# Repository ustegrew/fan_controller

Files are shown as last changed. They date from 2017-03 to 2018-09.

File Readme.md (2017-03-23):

# Ventilator control for a laundry

A control system for a fan in a laundry drying room, to exchange humid air for dry air from outside.

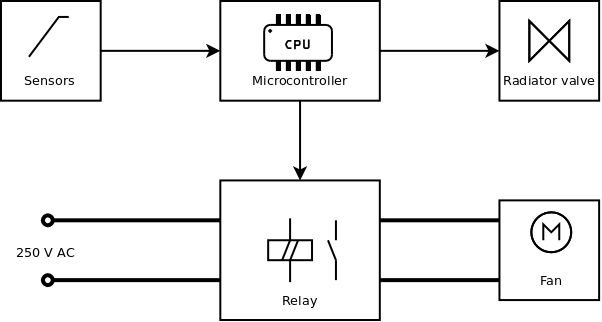
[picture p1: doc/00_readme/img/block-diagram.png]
Block diagram


## Repository structure

  * [Documentation::Wiki](https://github.com/ustegrew/fan_controller/wiki)
  * [Documentation::Files](https://github.com/ustegrew/fan_controller/tree/master/doc).

## Licenses

Source code is licensed under GPL3, all other content under FDL.

### Source code

    This program is free software: you can redistribute it and/or modify
    it under the terms of the GNU General Public License as published by
    the Free Software Foundation, either version 3 of the License, or
    (at your option) any later version.
	
    This program is distributed in the hope that it will be useful,
    but WITHOUT ANY WARRANTY; without even the implied warranty of
    MERCHANTABILITY or FITNESS FOR A PARTICULAR PURPOSE.  See the
    GNU General Public License for more details.
    
	You should have received a copy of the GNU General Public License
    along with this program.  If not, see <http://www.gnu.org/licenses/>.

### All other content

        Copyright (c)  2017  PETER HOPPE.
    Permission is granted to copy, distribute and/or modify this document
    under the terms of the GNU Free Documentation License, Version 1.3
    or any later version published by the Free Software Foundation;
    with no Invariant Sections, no Front-Cover Texts, and no Back-Cover Texts.
    A copy of the license is included in the section entitled "GNU
    Free Documentation License".

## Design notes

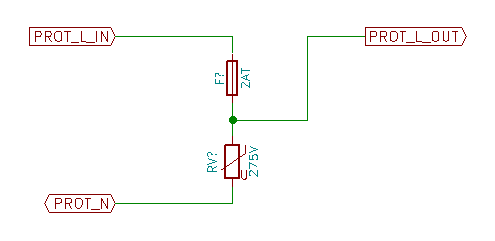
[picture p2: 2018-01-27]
schematics/controller/img/varistor-protection-module.png

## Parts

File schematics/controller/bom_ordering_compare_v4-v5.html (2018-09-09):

Article | Ref | Qnty | Value | Description
 | A15001 | 1 | Arduino_Nano_v3.x | Arduino Nano v3.x
Mouser::80-EST108M063AM3AA | C3001 | 1 | 1000uF/63V | Polarised capacitor
Mouser::594-MAL225098475E3 | C3002, C3006, C3010 | 3 | 470uF/63V | Polarised capacitor
Mouser::810-C3216C0G2A104J16 | C3003, C3007, C3008, C6002, C6003, C6006, C6007, C7002, C7003, C7005, C7008, C9002, C9003, C9006, C9007, C10002, C10003, C10005, C10008, C11005, C11006, C11013, C11014, C12001, C12002, C12003, C12005, C12006, C12007, C13001, C13004 | 31 | 100nF | Unpolarized capacitor
Mouser::810-C3216JB2A105K16A | C3004, C3005, C3009, C6008, C9008, C12009, C12010 | 7 | 1uF | Unpolarized capacitor
Mouser::667-EEU-EB1J470B | C5001, C5002, C7001, C7004, C8001, C8002, C10001, C10004, C11015, C11016, C12011, C12012, C13007, C13008 | 14 | 47uF / 63V | Polarised capacitor
Mouser::80-C1812C242GCG | C6001, C6005 | 2 | 2.4nF | Unpolarized capacitor
Mouser::810-C3225X7S2A475KST | C6004, C7006, C7007, C7009, C7010, C9004, C10006, C10007, C10009, C10010, C11007, C11012, C13002, C13005 | 14 | 4.7uF | Unpolarized capacitor
Mouser::80-C1206C474K1RAUTO | C6009, C9009 | 2 | 0.47uF | Unpolarized capacitor
Mouser::80-C2220C102FCG | C9001, C9005, C11001, C11002, C11004, C11008, C11009, C11011 | 8 | 1nF | Unpolarized capacitor
Mouser::80-C1206C911FBGACTU | C11003, C11010 | 2 | 910pF | Unpolarized capacitor
Mouser:: 80-C0805C224J1RECTU | C12004 | 1 | 0.22uF | Unpolarized capacitor
Mouser:: 80-C0805C393K1RAUTO | C12008 | 1 | 39nF | Unpolarized capacitor
Mouser::605-502S47W472KV4E | C13003, C13006 | 2 | 4.7nF | Unpolarized capacitor
Mouser::750-1.5KE33CA-G | D1001, D1002, D1003, D1004, D1005, D1006, D1007, D1008, D1009 | 9 | 1.5KE33CA | Bidirectional transient-voltage-suppression (TVS) diode
Mouser::78-1.5KE30CAHE3_A/C | D1010, D1011, D1012, D1013, D1014, D1015, D1016, D1017, D1018 | 9 | 1.5KE30CA | Bidirectional transient-voltage-suppression (TVS) diode
Mouser::78-1N4148W-E3-18 | D2001, D6001, D6002, D7003, D9001, D9002, D10003, D12002, D12003, D12004, D14001 | 11 | 1N4148 | 100V 0.15A standard switching diode, DO-35
Mouser::78-1.5KE36CAHE3_A/C | D3001, D3004, D3007, D3009, D3012, D3015, D3020, D3024 | 8 | 1.5KE36CA | Bidirectional transient-voltage-suppression (TVS) diode
Mouser::625-1N5404-E3 | D3002, D3003, D3005, D3006, D3010, D3011, D3013, D3014, D3018, D3019, D3021, D3022 | 12 | 1N5404 | 50V 3A General Purpose Rectifier Diode, DO-201AD
Mouser::621-1N4007G-T | D3008, D3016, D3023 | 3 | 1N4007 | 50V 1A General Purpose Rectifier Diode, DO-41
Mouser::625-BZX85C5V6 | D7001, D7002, D7004, D10001, D10002, D10004 | 6 | BZX85C5V6 | Zener Diode
Mouser::625-BZX85C6V2 | D12001 | 1 | BZX85C6V2 | z-diode, bzx85 series
Mouser::625-1.5KE12CA-E3 | D13001, D13002, D13003 | 3 | 1.5KE12CA | Bidirectional transient-voltage-suppression (TVS) diode
Mouser::576-64600001003 | F1001, F1002, F1003, F1004, F1005, F1006 | 6 | 250mAF | Fuse, generic
Mouser::576-64600001003 | F1007, F1008, F1009, F1010, F1011, F1012 | 6 | 100mAF | Fuse, generic
Mouser::534-4525 | F2001 | 1 | 6AT | Fuse, generic
Mouser::576-64600001003 | F3001, F3002 | 2 | 2AT | Fuse, generic
Mouser::576-64600001003 | F3003, F3004 | 2 | 1AT | Fuse, generic
Mouser::576-64600001003 | F3005, F3006, F3007, F3008 | 4 | 1AF | Fuse, generic
Mouser::651-5430373 | J1001, J1002 | 2 | Screw_Terminal_01x03 | Generic screw terminal, single row, 01x03
Mouser::651-1935268 | J1003 | 1 | Periphery | Generic screw terminal, single row, 01x12
Mouser::571-1969799-1 | J1004 | 1 | Conn_01x02_Male | Generic connector, single row, 01x02
Mouser::571-1969807-1 | J1005, J1006 | 2 | Conn_01x04_Male | Generic connector, single row, 01x04
Mouser::571-6404565 | J1007 | 1 | FRONTPANEL | Generic connector, single row, 01x05
Mouser::655-RT424024 | K2001 | 1 | TE RT424024 | General Purpose Relays DPDT 8A 24VDC PCB
inherent | MK1001, MK1002, MK1003, MK1004, MK1005, MK1006, MK1007, MK1008, MK1009, MK1010 | 10 | 3.5 | Mounting Hole with connection
Mouser::512-BC556BTA | Q2001, Q7004, Q10004, Q12001, Q12002 | 5 | BC556 | 45V Vce, 0.1A Ic, PNP Small Signal Transistor, TO-92
Mouser::512-BC546CTA | Q2002, Q7001, Q7002, Q7003, Q10001, Q10002, Q10003, Q12003, Q12004, Q12005, Q12006, Q12007, Q12008, Q14001, Q14002, Q14003, Q14004, Q14005, Q15001 | 19 | BC546C | 45V Vce, 0.1A Ic, NPN, Small Signal Transistor, TO-92
Mouser::863-BD243CG | Q2003 | 1 | BD243C | 25A Ic, 55V Vce, Silicon Power Transistors NPN, SOT-93
Not Mouser | Q6001, Q9001 | 2 | 2N3819 | Transistor N-JFET (general)
Mouser::594-AC01W27R00J | R1001, R1002, R1003, R1004, R1005, R1006 | 6 | 27Ω / 1W | Resistor
Mouser::71-TNPU0805100KAZEN | R2001, R2005, R7005, R7006, R7008, R7009, R7016, R10005, R10006, R10008, R10009, R10016, R11003, R12009, R12010, R12013, R12017, R12018, R13004, R13005, R14002, R14003, R14007, R14009, R14010 | 25 | 100kΩ | Resistor
Mouser::71-TNPU080510K0AZEN | R2002, R2003, R7002, R7003, R7004, R7007, R10002, R10003, R10004, R10007, R13001, R13002, R14001, R14004, R14005, R14006, R14008, R15001, R15002, R15003, R15004, R15005, R15006, R15007 | 24 | 10kΩ | Resistor
Mouser::594-MCU08050C4701FP5 | R2004, R6003, R6004, R7001, R7010, R9003, R9004, R10001, R10010, R12001 | 10 | 4.7kΩ | Resistor
Mouser::71-TNPW06034K42BEEA | R6001, R6002 | 2 | 4.42kΩ | Resistor
Mouser::71-TNPU08051K00BZEN | R7011, R7012, R7013, R7014, R7015, R10011, R10012, R10013, R10014, R10015 | 10 | 1kΩ | Resistor
Mouser::71-TNPW06036K34BEEN | R9001, R9002 | 2 | 6.34kΩ | Resistor
Mouser::71-TNPW0603118KBEEN | R11001, R11004 | 2 | 118kΩ | Resistor
Mouser::71-TNPW0603133KBEEN | R11002 | 1 | 133kΩ | Resistor
Mouser::71-TNPU080549K9BZEN | R11005 | 1 | 49.9kΩ | Resistor
Mouser::71-TNPW060356K2BEEA | R11006 | 1 | 56.2kΩ | Resistor
Mouser::71-TNPW060339K2BEEN | R11007 | 1 | 39.2kΩ | Resistor
Mouser::71-TNPW060346K4BEEA | R11008 | 1 | 46.4kΩ | Resistor
Mouser::71-TNPW0603825RBEEA | R11009 | 1 | 825Ω | Resistor
Mouser::71-TNPW0603931RBEEN | R11010 | 1 | 931Ω | Resistor
Mouser::71-TNPW06031K05BEEA | R11011 | 1 | 1.05kΩ | Resistor
Mouser::71-TNPW060323K7BEEN | R11012 | 1 | 23.7kΩ | Resistor
Mouser::71-TNPW06031K21BEEN | R11013 | 1 | 1.21kΩ | Resistor
Mouser::71-TNPW060327K4BEEN | R11014 | 1 | 27.4kΩ | Resistor
Mouser::71-TNPW0603316RBEEN | R11015 | 1 | 316Ω | Resistor
Mouser::71-TNPW0603357RBEEA | R11016 | 1 | 357Ω | Resistor
Mouser::71-TNPW060368K0BEEA | R12002 | 1 | 68kΩ | Resistor
Mouser::71-TNPW060322K0BEEN | R12003, R12004, R12006, R12007, R12008 | 5 | 22kΩ | Resistor
Mouser::71-TNPW06037K50BEEN | R12005 | 1 | 7.5kΩ | Resistor
Mouser::71-TNPW060339K0BEEA | R12011, R12012, R12014, R12015, R12016, R12019 | 6 | 39kΩ | Resistor
Mouser::71-TNPW0603220RBEEA | R13003, R13006 | 2 | 220Ω | Resistor
Mouser::652-3296W-1-223LF | RV6001, RV6002, RV9001, RV9002, RV12001, RV13001, RV13002 | 7 | 22kΩ | Potentiometer
alreadyHere::Mouser::983-T60403-K5032X102 | T13001 | 1 | Transformer_2P_1S | Transformer, single primary, dual secondary
Mouser::571-1969803-1 | U1001 | 1 | Module: surgeprot.mains.275.5.01
Mouser::652-2026-07-C2LF | U1002, U1003, U1004 | 3 | Bourns 2026-07-C2LF | Gas discharge tube
Mouser::511-L7805ABV | U3001 | 1 | L7805 | Positive 1.5A 35V Linear Regulator, Fixed Output 5V, TO-220/TO-263/TO-252
Mouser::511-L7815ABV | U3002 | 1 | L7815 | Positive 1.5A 35V Linear Regulator, Fixed Output 5V, TO-220/TO-263/TO-252
Mouser::511-L7915ACV | U3003 | 1 | L7915 | Negative 1.5A 35V Linear Regulator, Fixed Output -5V, TO-220/TO-263
Mouser::595-TL061CDR | U6001, U6002, U7002, U9001, U9002, U10002, U12001, U12002, U12003 | 9 | TL061 | Operational Amplifier, DIP-8/TO-99-8
Mouser::595-CD4066BM96 | U7001, U10001 | 2 | 4066 | Quad Analog Switches
Mouser::584-OP282GSZ | U11001, U11002, U13001 | 3 | OP282 | Dual/Quad, Low Power, High Speed JFET Operational Amplifiers
Ref | Qnty | Value | Part | Footprint | Description | Vendor
A15001 | 1 | Arduino_Nano_v3.x | modules:Arduino_Nano_v3.x | footprints:arduino-nano_3.x | Arduino Nano v3.x
C3001 | 1 | 1000uF/63V | Device:CP | Capacitors_THT:CP_Radial_D16.0mm_P7.50mm | Polarised capacitor
C3002, C3006, C3010 | 3 | 470uF/63V | Device:CP | Capacitors_THT:CP_Radial_D16.0mm_P7.50mm | Polarised capacitor
C3003, C3007, C3008, C6002, C6003, C6006, C6007, C7002, C7003, C7005, C7008, C9002, C9003, C9006, C9007, C10002, C10003, C10005, C10008, C11005, C11006, C11013, C11014, C12001, C12002, C12003, C12005, C12006, C12007, C13001, C13004 | 31 | 100nF | Device:C | Capacitors_SMD:C_1206_HandSoldering | Unpolarized capacitor
C3004, C3005, C3009, C6008, C9008, C12009, C12010 | 7 | 1uF | Device:C | Capacitors_SMD:C_1206_HandSoldering | Unpolarized capacitor
C5001, C5002, C7001, C7004, C8001, C8002, C10001, C10004, C11015, C11016, C12011, C12012, C13007, C13008 | 14 | 47uF / 63V | Device:CP | Capacitors_THT:CP_Radial_D8.0mm_P5.00mm | Polarised capacitor
C6001, C6005 | 2 | 2.4nF | Device:C | Capacitors_SMD:C_1812_HandSoldering | Unpolarized capacitor
C6004, C7006, C7007, C7009, C7010, C9004, C10006, C10007, C10009, C10010, C11007, C11012, C13002, C13005 | 14 | 4.7uF | Device:C | Capacitors_SMD:C_1210_HandSoldering | Unpolarized capacitor
C6009, C9009 | 2 | 0.47uF | Device:C | Capacitors_SMD:C_1206_HandSoldering | Unpolarized capacitor
C9001, C9005, C11001, C11002, C11004, C11008, C11009, C11011 | 8 | 1nF | Device:C | Capacitors_SMD:C_2220_HandSoldering | Unpolarized capacitor
C11003, C11010 | 2 | 910pF | Device:C | Capacitors_SMD:C_1206_HandSoldering | Unpolarized capacitor
C12004 | 1 | 0.22uF | Device:C | Capacitors_SMD:C_0805_HandSoldering | Unpolarized capacitor
C12008 | 1 | 39nF | Device:C | Capacitors_SMD:C_0805_HandSoldering | Unpolarized capacitor
C13003, C13006 | 2 | 4.7nF | Device:C | Capacitors_SMD:C_2220_HandSoldering | Unpolarized capacitor
D1001, D1002, D1003, D1004, D1005, D1006, D1007, D1008, D1009 | 9 | 1.5KE33CA | Device:D_TVS | Diodes_THT:D_DO-201AD_P12.70mm_Horizontal | Bidirectional transient-voltage-suppression (TVS) diode
D1010, D1011, D1012, D1013, D1014, D1015, D1016, D1017, D1018 | 9 | 1.5KE30CA | Device:D_TVS | Diodes_THT:D_DO-201AD_P12.70mm_Horizontal | Bidirectional transient-voltage-suppression (TVS) diode
D2001, D6001, D6002, D7003, D9001, D9002, D10003, D12002, D12003, D12004, D14001 | 11 | 1N4148 | diode:1N4148 | Diodes_SMD:D_SOD-123 | 100V 0.15A standard switching diode, DO-35
D3001, D3004, D3007, D3009, D3012, D3015, D3020, D3024 | 8 | 1.5KE36CA | Device:D_TVS | Diodes_THT:D_DO-201AD_P12.70mm_Horizontal | Bidirectional transient-voltage-suppression (TVS) diode
D3002, D3003, D3005, D3006, D3010, D3011, D3013, D3014, D3018, D3019, D3021, D3022 | 12 | 1N5404 | diode:1N5404 | Diodes_THT:D_DO-201AD_P12.70mm_Horizontal | 400V 3A General Purpose Rectifier Diode, DO-201AD
D3008, D3016, D3023 | 3 | 1N4007 | diode:1N4007 | Diodes_THT:D_DO-41_SOD81_P7.62mm_Horizontal | 1000V 1A General Purpose Rectifier Diode, DO-41
D7001, D7002, D7004, D10001, D10002, D10004 | 6 | BZX85C5V6 | Device:D_Zener | Diodes_THT:D_DO-41_SOD81_P7.62mm_Horizontal | Zener Diode
D12001 | 1 | BZX85C6V2 | fan-controller_parts:BZX85xx | Diodes_THT:D_DO-41_SOD81_P7.62mm_Horizontal | z-diode, bzx85 series
D13001, D13002, D13003 | 3 | 1.5KE12CA | Device:D_TVS | Diodes_THT:D_DO-201AD_P12.70mm_Horizontal | Bidirectional transient-voltage-suppression (TVS) diode
F1001, F1002, F1003, F1004, F1005, F1006 | 6 | 250mAF | Device:Fuse | Fuse_Holders_and_Fuses:Fuseholder5x20_horiz_open_Schurter_0031_8201 | Fuse, generic
F1007, F1008, F1009, F1010, F1011, F1012 | 6 | 100mAF | Device:Fuse | Fuse_Holders_and_Fuses:Fuseholder5x20_horiz_open_Schurter_0031_8201 | Fuse, generic
F2001 | 1 | 6AT | Device:Fuse | Wire_Connections_Bridges:WireConnection_2.50mmDrill_LargePad | Fuse, generic
F3001, F3002 | 2 | 2AT | Device:Fuse | Fuse_Holders_and_Fuses:Fuseholder5x20_horiz_open_Schurter_0031_8201 | Fuse, generic
F3003, F3004 | 2 | 1AT | Device:Fuse | Fuse_Holders_and_Fuses:Fuseholder5x20_horiz_open_Schurter_0031_8201 | Fuse, generic
F3005, F3006, F3007, F3008 | 4 | 1AF | Device:Fuse | Fuse_Holders_and_Fuses:Fuseholder5x20_horiz_open_Schurter_0031_8201 | Fuse, generic
J1001, J1002 | 2 | Screw_Terminal_01x03 | conn:Screw_Terminal_01x03 | Connectors_Phoenix:PhoenixContact_MSTBVA-G_03x5.00mm_Vertical | Generic screw terminal, single row, 01x03
J1003 | 1 | Periphery | conn:Screw_Terminal_01x12 | Connectors_Phoenix:PhoenixContact_MSTBVA-G_12x5.00mm_Vertical | Generic screw terminal, single row, 01x12
J1004 | 1 | Conn_01x02_Male | conn:Conn_01x02_Male | footprints:TE_1969799-1 | Generic connector, single row, 01x02
J1005, J1006 | 2 | Conn_01x04_Male | conn:Conn_01x04_Male | footprints:TE_1969807-1 | Generic connector, single row, 01x04
J1007 | 1 | FRONTPANEL | conn:Conn_01x05_Male | Pin_Headers:Pin_Header_Straight_1x05_Pitch2.54mm | Generic connector, single row, 01x05
K2001 | 1 | TE RT424024 (24VDC@1.44kOhm, DPDT, 250VAC, 8A) | relays:FINDER-44.62 | footprints:Relay_DPDT_Schrack-RT2-FormC_RM5.04mm | FINDER 44.62, Dual Pole Relay, 5mm Pitch, 10A
MK1001, MK1002, MK1003, MK1004, MK1005, MK1006, MK1007, MK1008, MK1009, MK1010 | 10 | 3.5 | mechanical:Mounting_Hole_PAD | Mounting_Holes:MountingHole_3.5mm_Pad_Via | Mounting Hole with connection
Q2001, Q7004, Q10004, Q12001, Q12002 | 5 | BC556 | Transistor_BJT:BC556 | TO_SOT_Packages_THT:TO-92_Inline_Wide | 0.1A Ic, 65V Vce, PNP Small Signal Transistor, TO-92
Q2002, Q7001, Q7002, Q7003, Q10001, Q10002, Q10003, Q12003, Q12004, Q12005, Q12006, Q12007, Q12008, Q14001, Q14002, Q14003, Q14004, Q14005, Q15001 | 19 | BC546C | transistors:BC546 | TO_SOT_Packages_THT:TO-92_Inline_Wide | 65V Vce, 0.1A Ic, NPN, Small Signal Transistor, TO-92
Q2003 | 1 | BD243C | transistors:BD249C | TO_SOT_Packages_THT:TO-220-3_Vertical | 25A Ic, 115V Vce, Silicon Power Transistors NPN, SOT-93
Q6001, Q9001 | 2 | 2N3819 | Device:Q_NJFET_DGS | TO_SOT_Packages_THT:TO-92_Inline_Wide | Transistor N-JFET (general)
R1001, R1002, R1003, R1004, R1005, R1006 | 6 | 27Ω / 1W | device:R | Resistors_THT:R_Axial_DIN0414_L11.9mm_D4.5mm_P15.24mm_Horizontal | Resistor
R2001, R2005, R7005, R7006, R7008, R7009, R7016, R10005, R10006, R10008, R10009, R10016, R11003, R12009, R12010, R12013, R12017, R12018, R13004, R13005, R14002, R14003, R14007, R14009, R14010 | 25 | 100kΩ | device:R | Resistors_SMD:R_0805_HandSoldering | Resistor
R2002, R2003, R7002, R7003, R7004, R7007, R10002, R10003, R10004, R10007, R13001, R13002, R14001, R14004, R14005, R14006, R14008, R15001, R15002, R15003, R15004, R15005, R15006, R15007 | 24 | 10kΩ | device:R | Resistors_SMD:R_0805_HandSoldering | Resistor
R2004, R6003, R6004, R7001, R7010, R9003, R9004, R10001, R10010, R12001 | 10 | 4.7kΩ | device:R | Resistors_SMD:R_0805_HandSoldering | Resistor
R6001, R6002 | 2 | 4.42kΩ | Device:R | Resistors_SMD:R_0603_HandSoldering | Resistor
R7011, R7012, R7013, R7014, R7015, R10011, R10012, R10013, R10014, R10015 | 10 | 1kΩ | Device:R | Resistors_SMD:R_0805_HandSoldering | Resistor
R9001, R9002 | 2 | 6.34kΩ | Device:R | Resistors_SMD:R_0603_HandSoldering | Resistor
R11001, R11004 | 2 | 118kΩ | device:R | Resistors_SMD:R_0603_HandSoldering | Resistor
R11002 | 1 | 133kΩ | device:R | Resistors_SMD:R_0603_HandSoldering | Resistor
R11005 | 1 | 49.9kΩ | device:R | Resistors_SMD:R_0805_HandSoldering | Resistor
R11006 | 1 | 56.2kΩ | device:R | Resistors_SMD:R_0603_HandSoldering | Resistor
R11007 | 1 | 39.2kΩ | device:R | Resistors_SMD:R_0603_HandSoldering | Resistor
R11008 | 1 | 46.4kΩ | device:R | Resistors_SMD:R_0603_HandSoldering | Resistor
R11009 | 1 | 825Ω | device:R | Resistors_SMD:R_0603_HandSoldering | Resistor
R11010 | 1 | 931Ω | device:R | Resistors_SMD:R_0603_HandSoldering | Resistor
R11011 | 1 | 1.05kΩ | device:R | Resistors_SMD:R_0603_HandSoldering | Resistor
R11012 | 1 | 23.7kΩ | device:R | Resistors_SMD:R_0603_HandSoldering | Resistor
R11013 | 1 | 1.21kΩ | device:R | Resistors_SMD:R_0603_HandSoldering | Resistor
R11014 | 1 | 27.4kΩ | device:R | Resistors_SMD:R_0603_HandSoldering | Resistor
R11015 | 1 | 316Ω | device:R | Resistors_SMD:R_0603_HandSoldering | Resistor
R11016 | 1 | 357Ω | device:R | Resistors_SMD:R_0603_HandSoldering | Resistor
R12002 | 1 | 68kΩ | device:R | Resistors_SMD:R_0603_HandSoldering | Resistor
R12003, R12004, R12006, R12007, R12008 | 5 | 22kΩ | device:R | Resistors_SMD:R_0603_HandSoldering | Resistor
R12005 | 1 | 7.5kΩ | device:R | Resistors_SMD:R_0603_HandSoldering | Resistor
R12011, R12012, R12014, R12015, R12016, R12019 | 6 | 39kΩ | device:R | Resistors_SMD:R_0603_HandSoldering | Resistor
R13003, R13006 | 2 | 220Ω | device:R | Resistors_SMD:R_0603_HandSoldering | Resistor
RV6001, RV6002, RV9001, RV9002, RV12001, RV13001, RV13002 | 7 | 22kΩ | device:POT_TRIM | Potentiometers:Potentiometer_Trimmer_Bourns_3296W | Trim-Potentiometer
T13001 | 1 | Transformer_2P_1S | Device:Transformer_1P_2S | fan-controller_parts:TRANSFORMER_VENDOR_VACUUMSCHMELZE_T60403-K5032-X102 | Transformer, single primary, dual secondary
U1001 | 1 | Module: surgeprot.mains.275.5.01 | fan-controller_parts:line-protector | footprints:TE_1969803-1
U1002, U1003, U1004 | 3 | Bourns 2026-07-C2LF | ESD_Protection:GDT-3 | footprints:Bourns_2026-xx | Gas discharge tube
U3001 | 1 | L7805 | regul:L7805 | Power_Integrations:TO-220 | Positive 1.5A 35V Linear Regulator, Fixed Output 5V, TO-220/TO-263/TO-252
U3002 | 1 | L7815 | regul:L7815 | Power_Integrations:TO-220 | Positive 1.5A 35V Linear Regulator, Fixed Output 15V, TO-220/TO-263/TO-252
U3003 | 1 | L7915 | regul:L7915 | Power_Integrations:TO-220 | Negative 1.5A 35V Linear Regulator, Fixed Output -15V, TO-220/TO-263
U6001, U6002, U7002, U9001, U9002, U10002, U12001, U12002, U12003 | 9 | TL061 | Amplifier_Operational:TL061 | Housings_SOIC:SOIC-8-1EP_3.9x4.9mm_Pitch1.27mm | Single Low-Power JFET-Input Operational Amplifiers, DIP-8/SOIC-8
U7001, U10001 | 2 | 4066 | 4xxx:4066 | Housings_SOIC:SOIC-14_3.9x8.7mm_Pitch1.27mm | Quad Analog Switches
U11001, U11002, U13001 | 3 | OP282 | fan-controller_parts:OP282 | Housings_SOIC:SOIC-8-1EP_3.9x4.9mm_Pitch1.27mm | Dual/Quad, Low Power, High Speed JFET Operational Amplifiers

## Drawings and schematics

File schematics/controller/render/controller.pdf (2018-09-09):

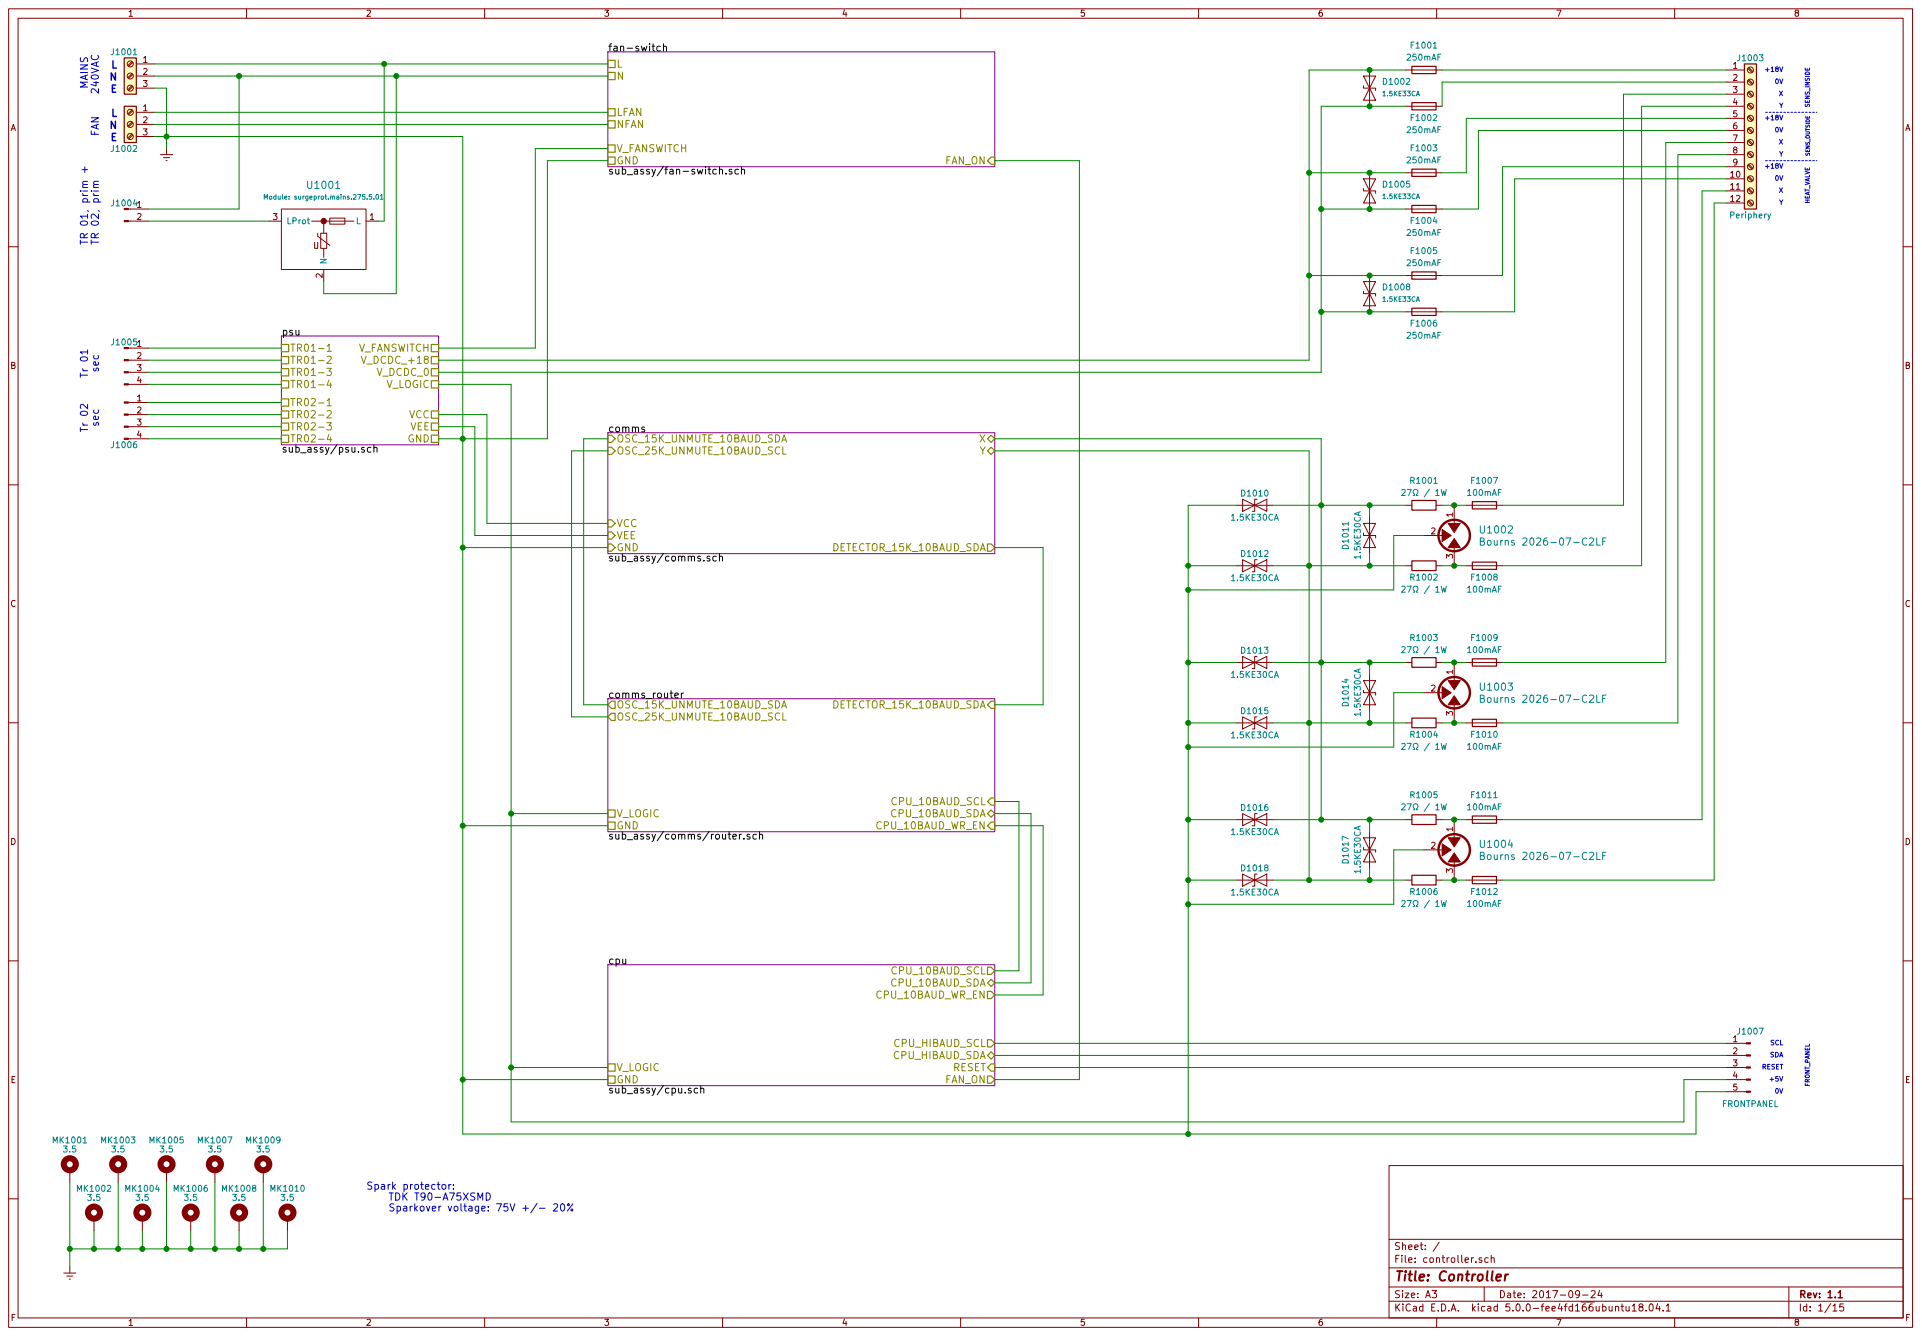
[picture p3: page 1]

Module: surgeprot.mains.275.5.01 MAINS 240VAC FAN

LN NFAN GND

10
11

100mAF D1016

Id: 1/15 Title: Controller File: controller.sch Sheet: /

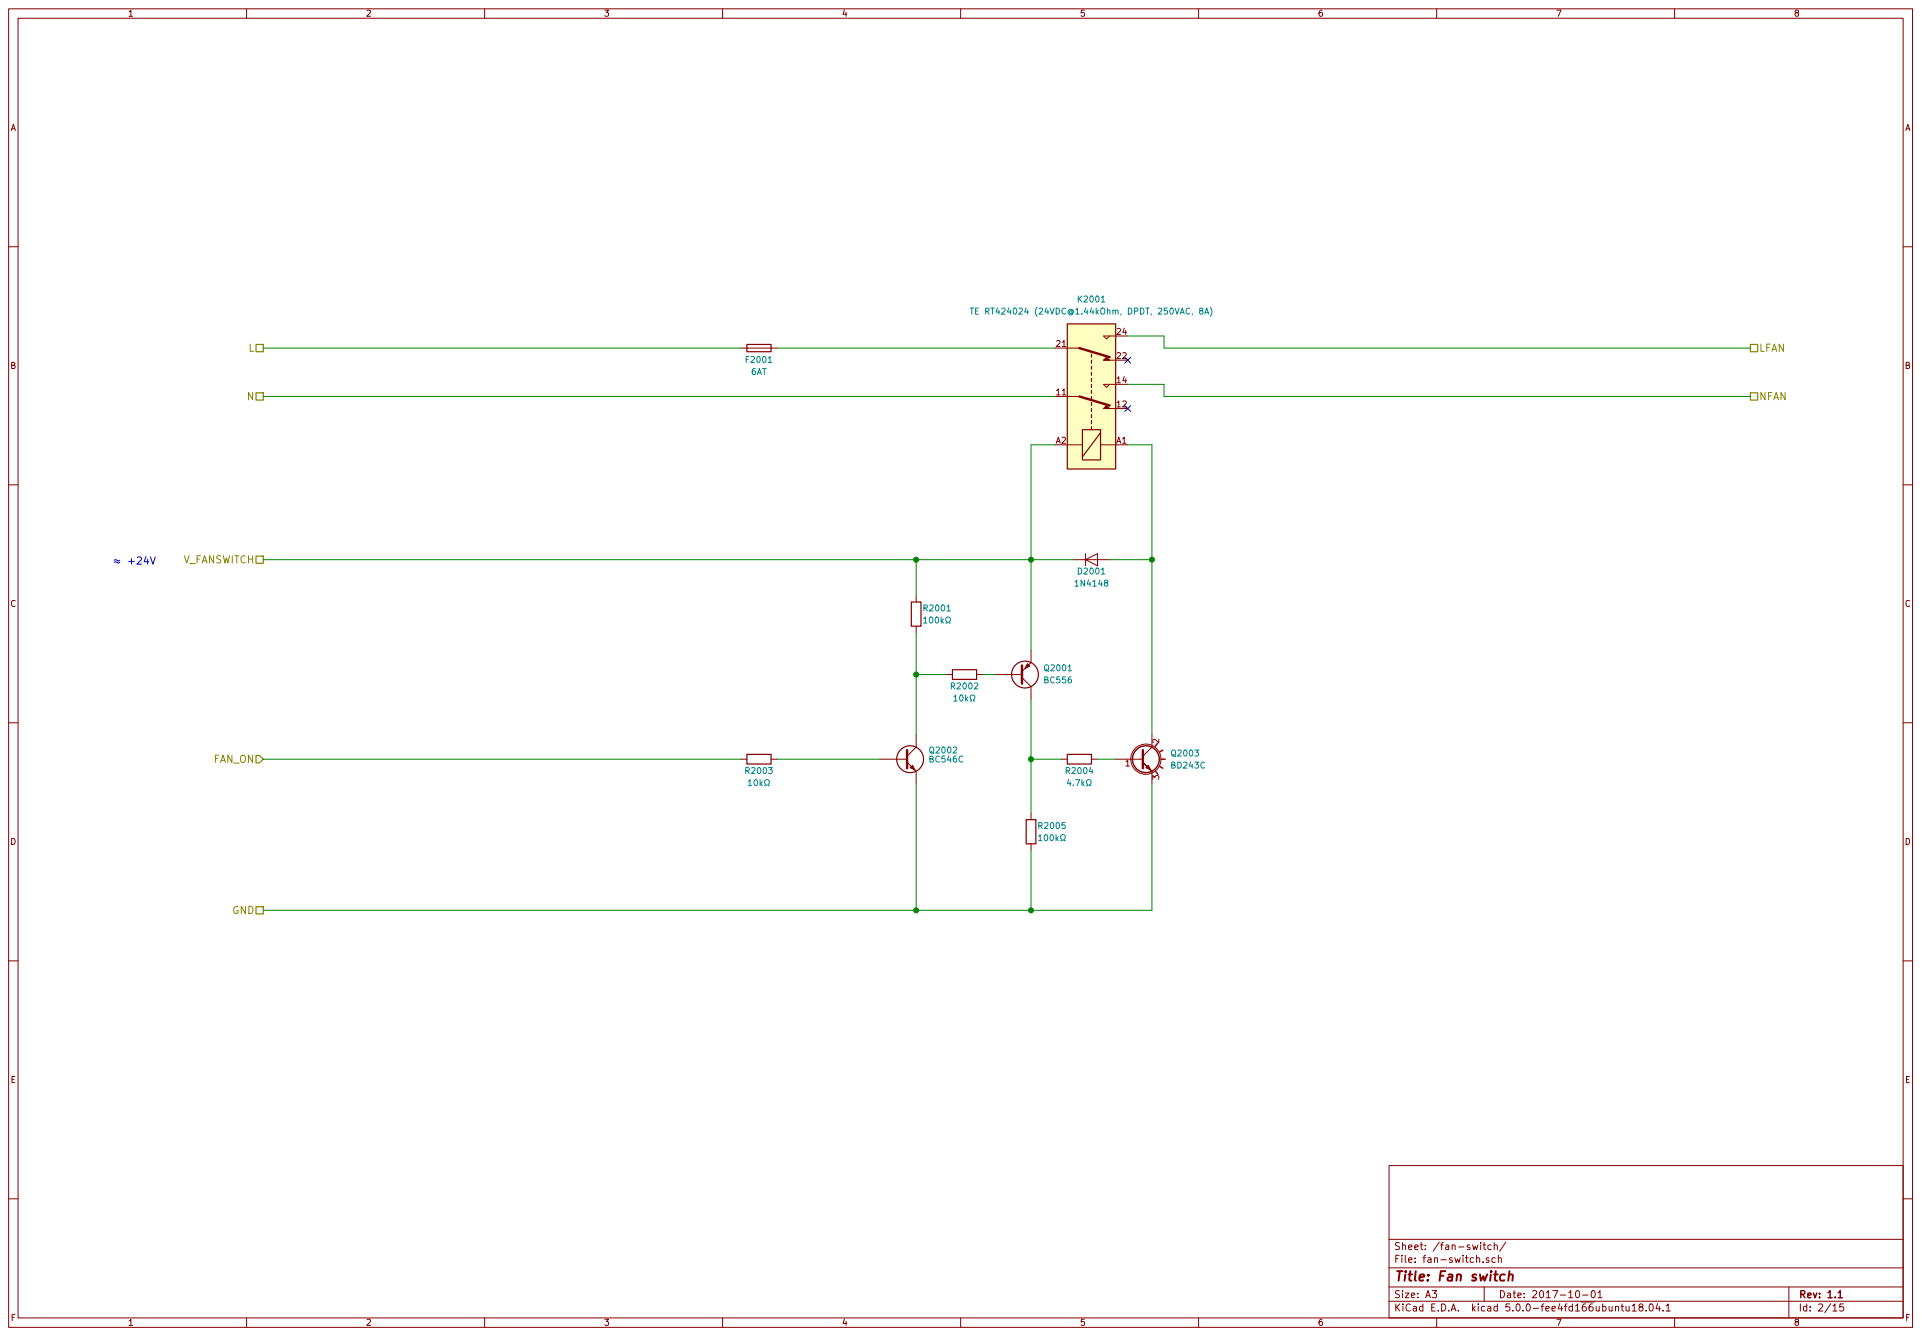
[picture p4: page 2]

File: fan-switch.sch Sheet: /fan-switch/
Id: 2/15 Title: Fan switch

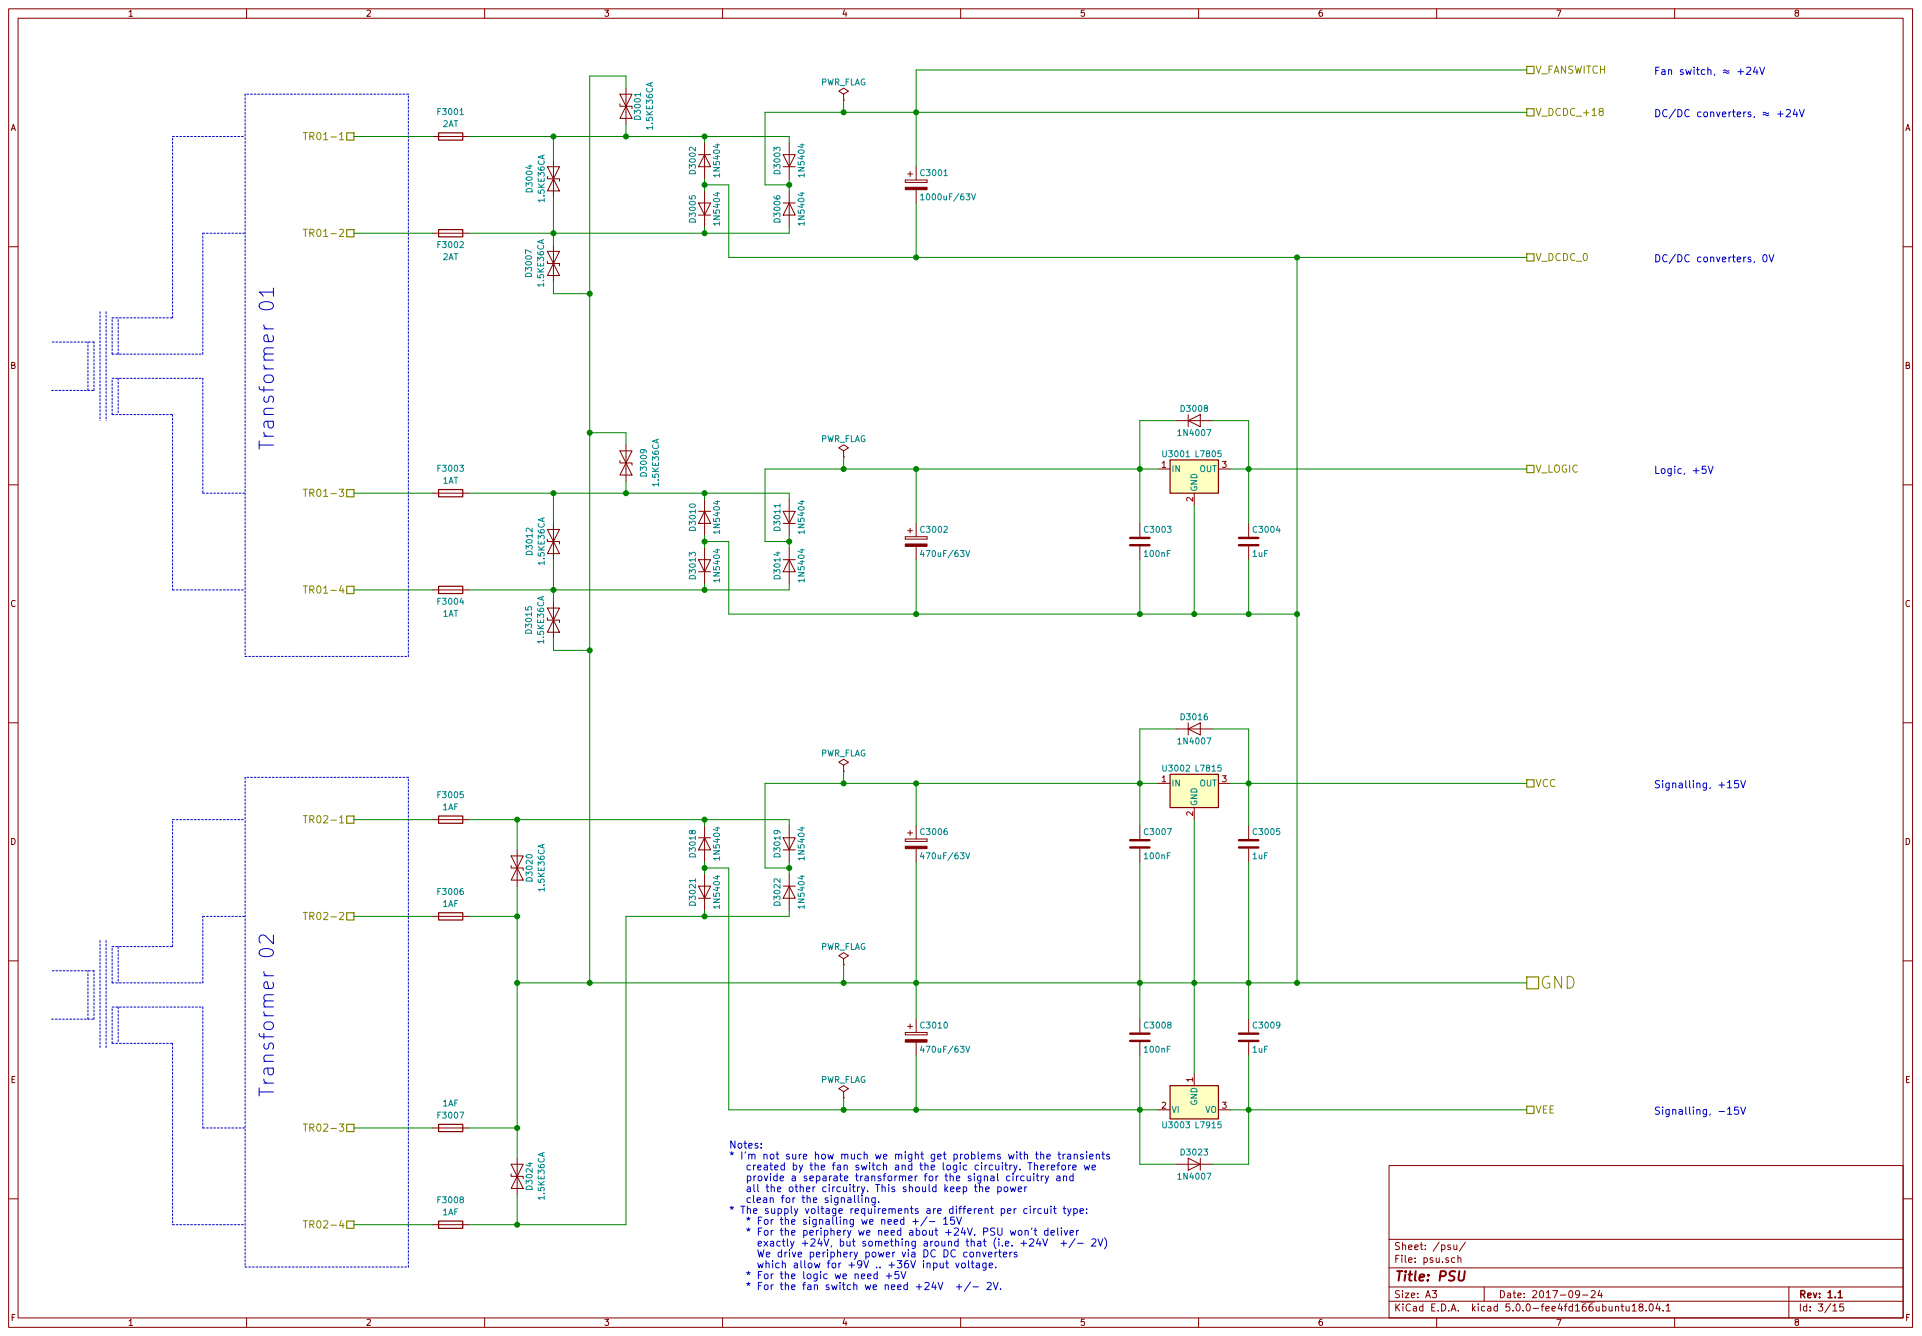
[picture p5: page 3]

PWR_FLAG Notes: * I'm not sure how much we might get problems with the transients

created by the fan switch and the logic circuitry. Therefore we
provide a separate transformer for the signal circuitry and
all the other circuitry. This should keep the power
clean for the signalling.
* The supply voltage requirements are different per circuit type:
* For the signalling we need +/- 15V
* For the periphery we need about +24V. PSU won't deliver
We drive periphery power via DC DC converters
which allow for +9V .. +36V input voltage.
* For the logic we need +5V
* For the fan switch we need +24V +/- 2V.

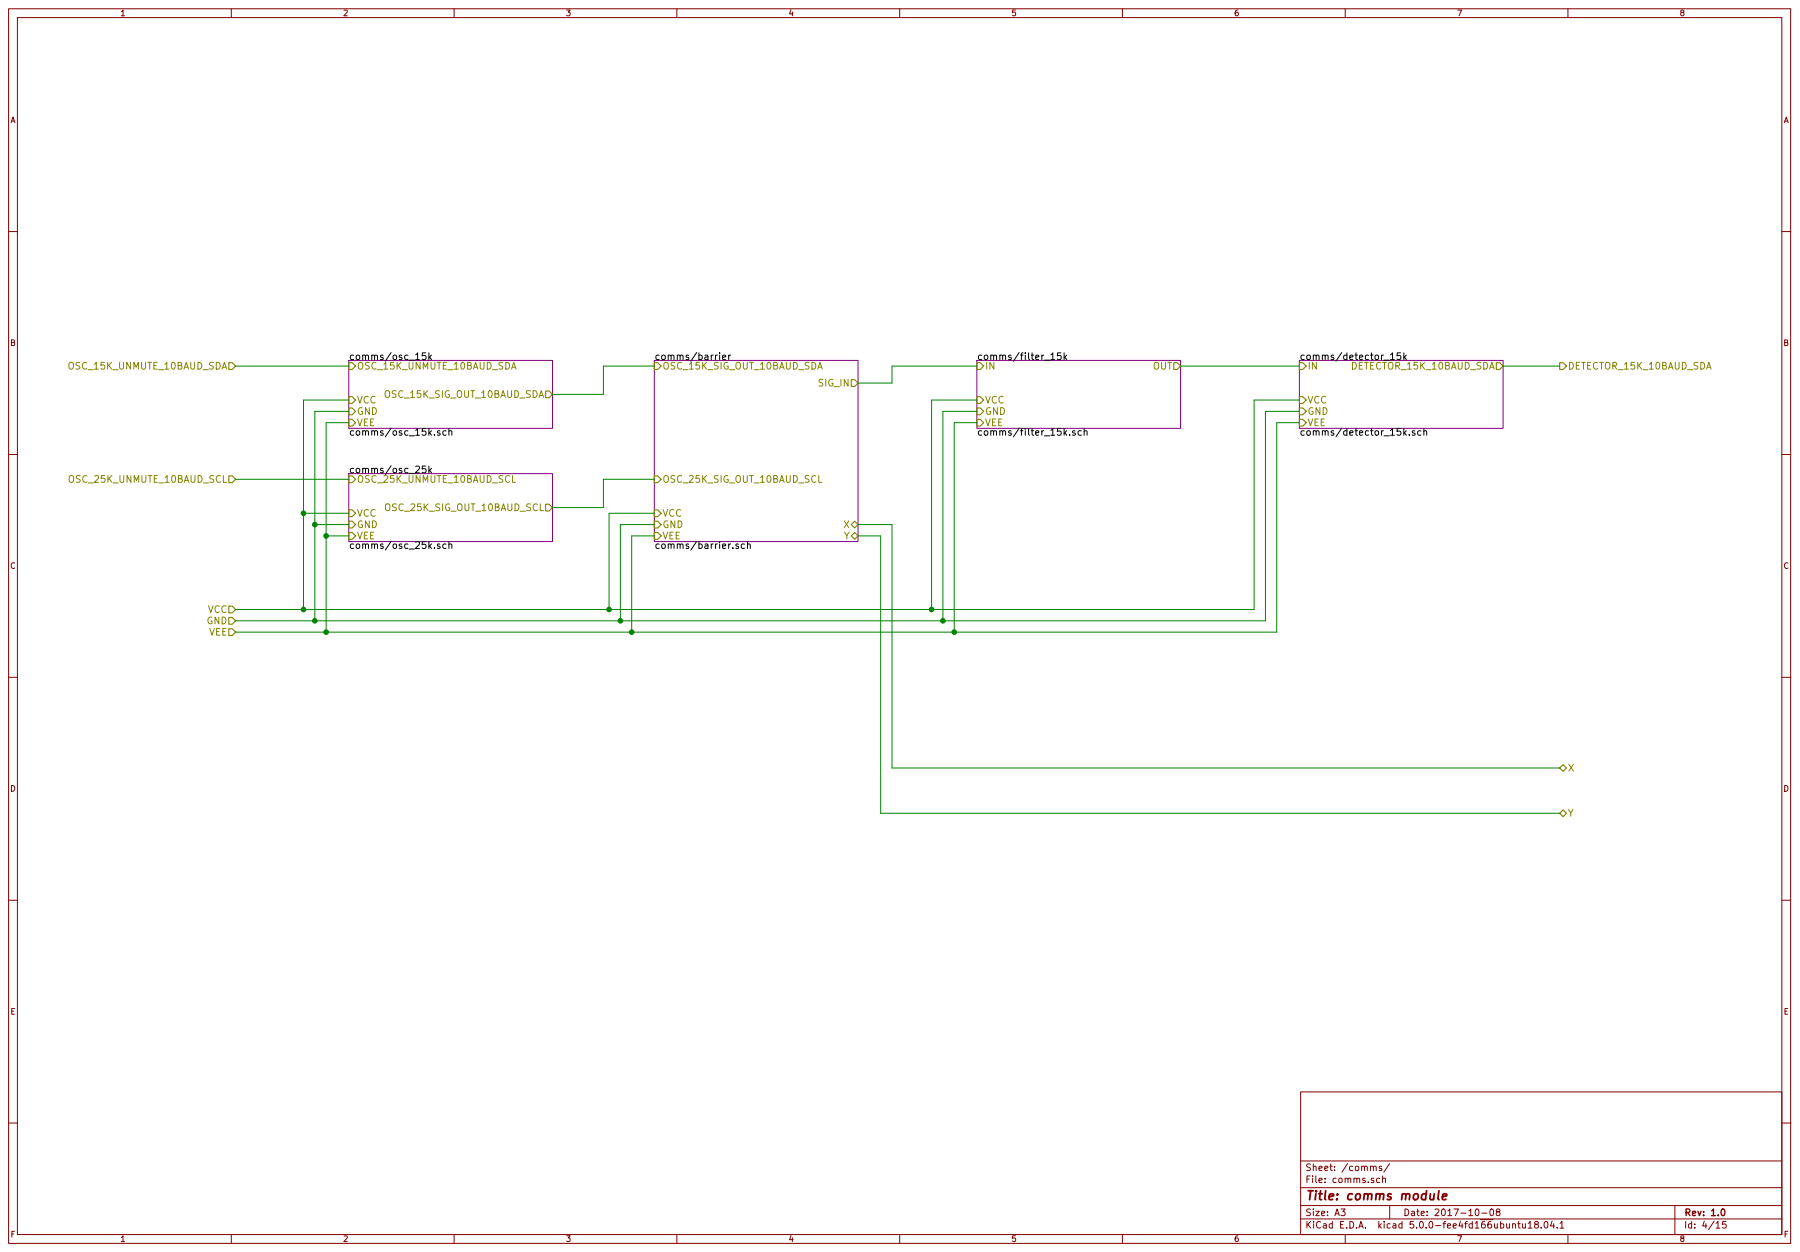
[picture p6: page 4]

File: comms.sch Sheet: /comms/
Id: 4/15 Title: comms module

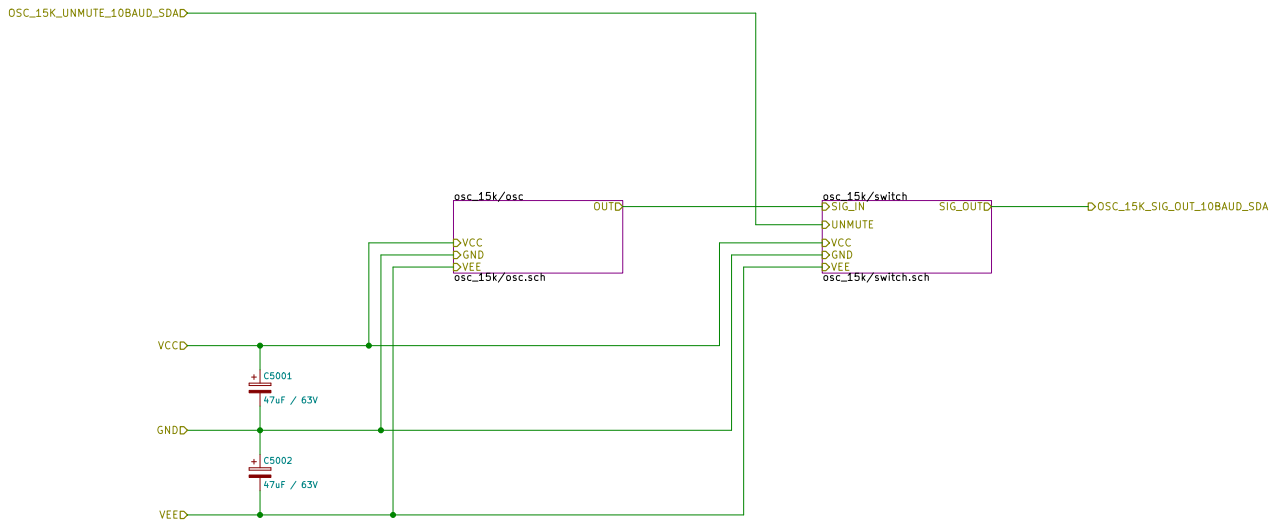
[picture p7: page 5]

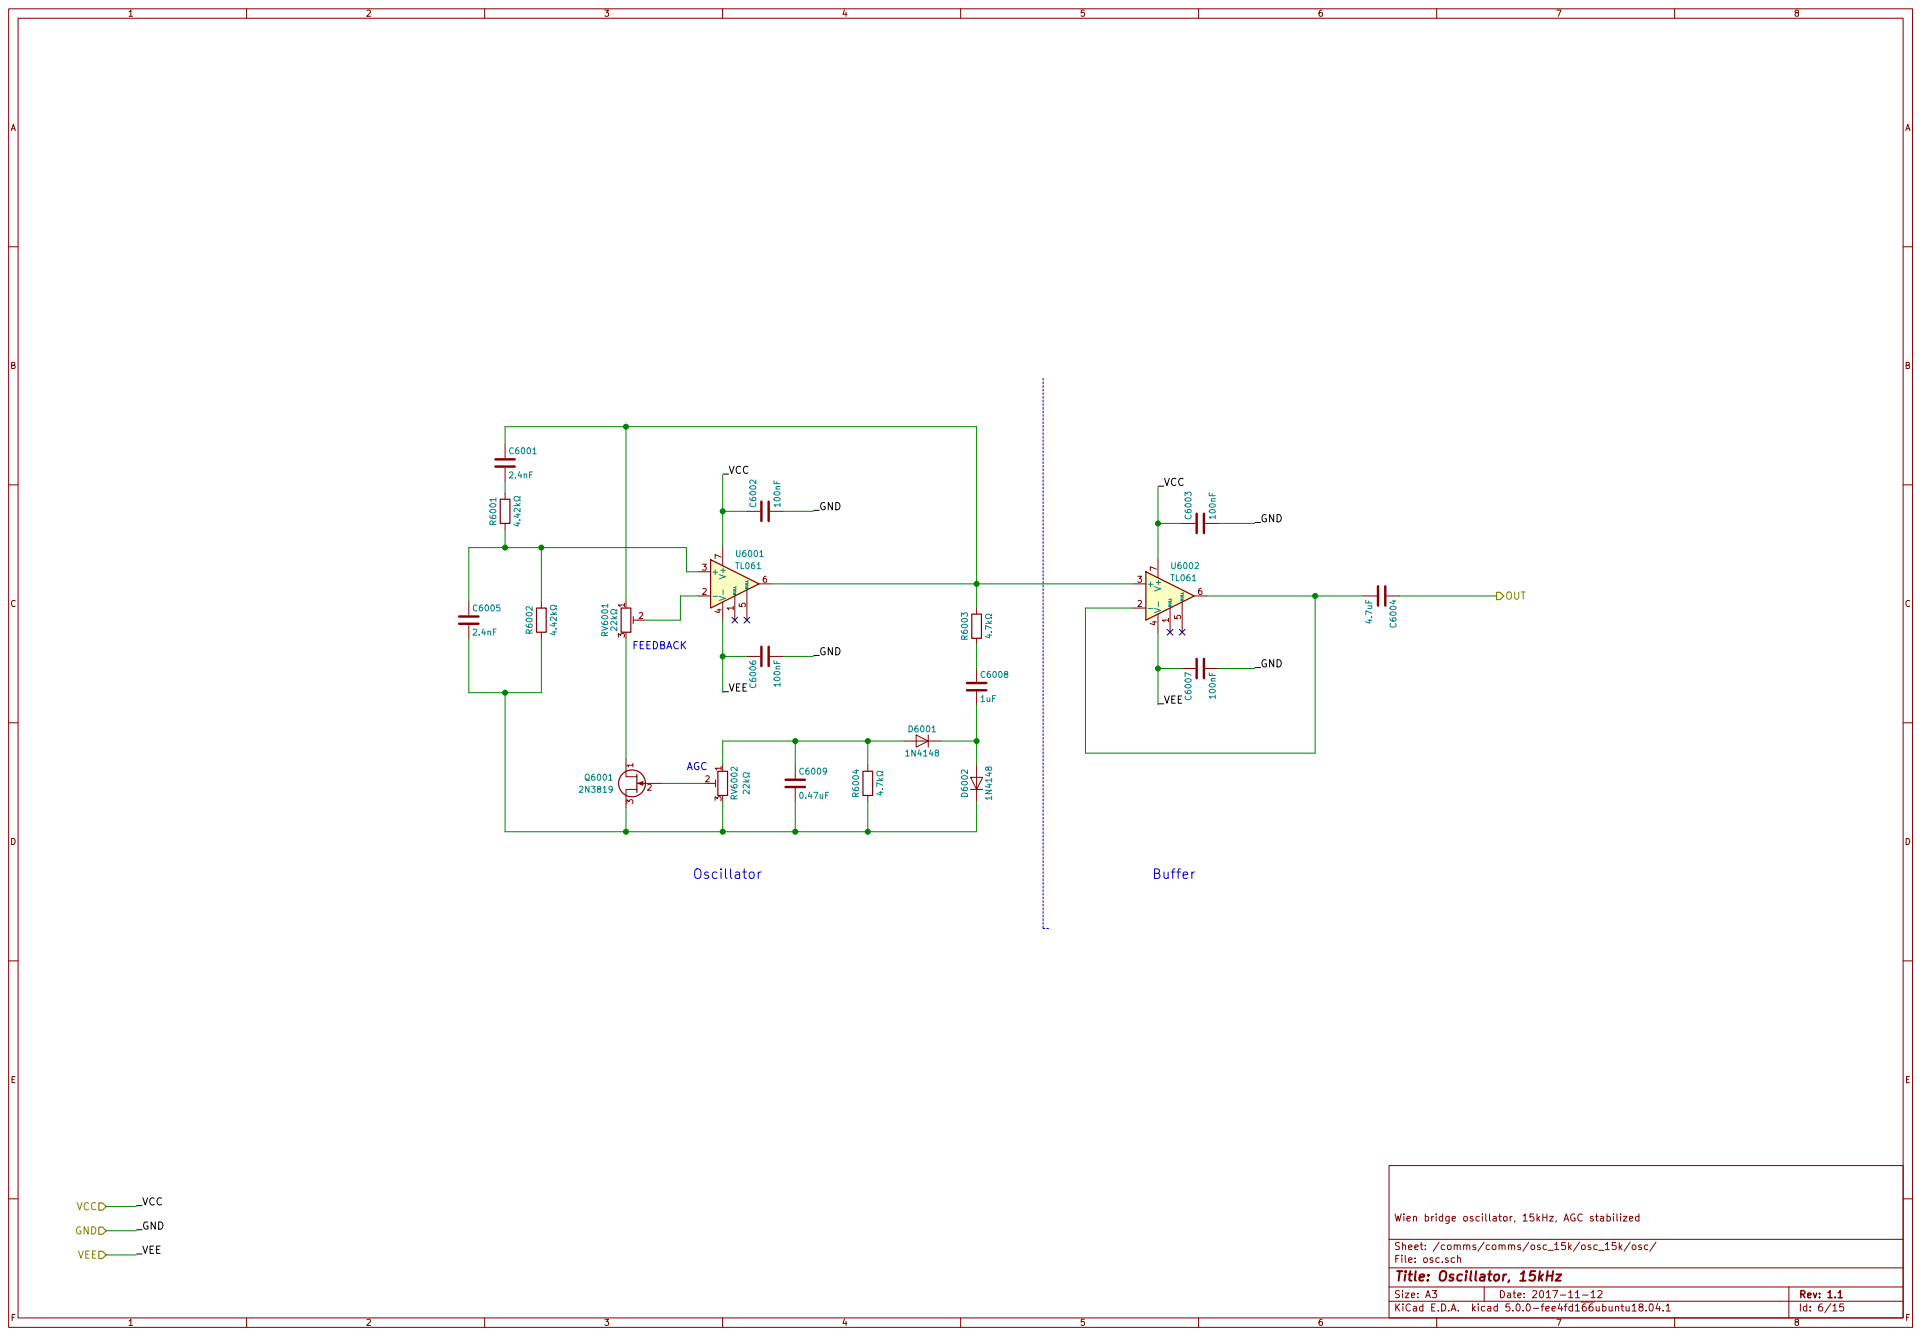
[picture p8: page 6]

File: osc.sch Sheet: /comms/comms/osc_15k/osc_15k/osc/
Id: 6/15 Title: Oscillator, 15kHz

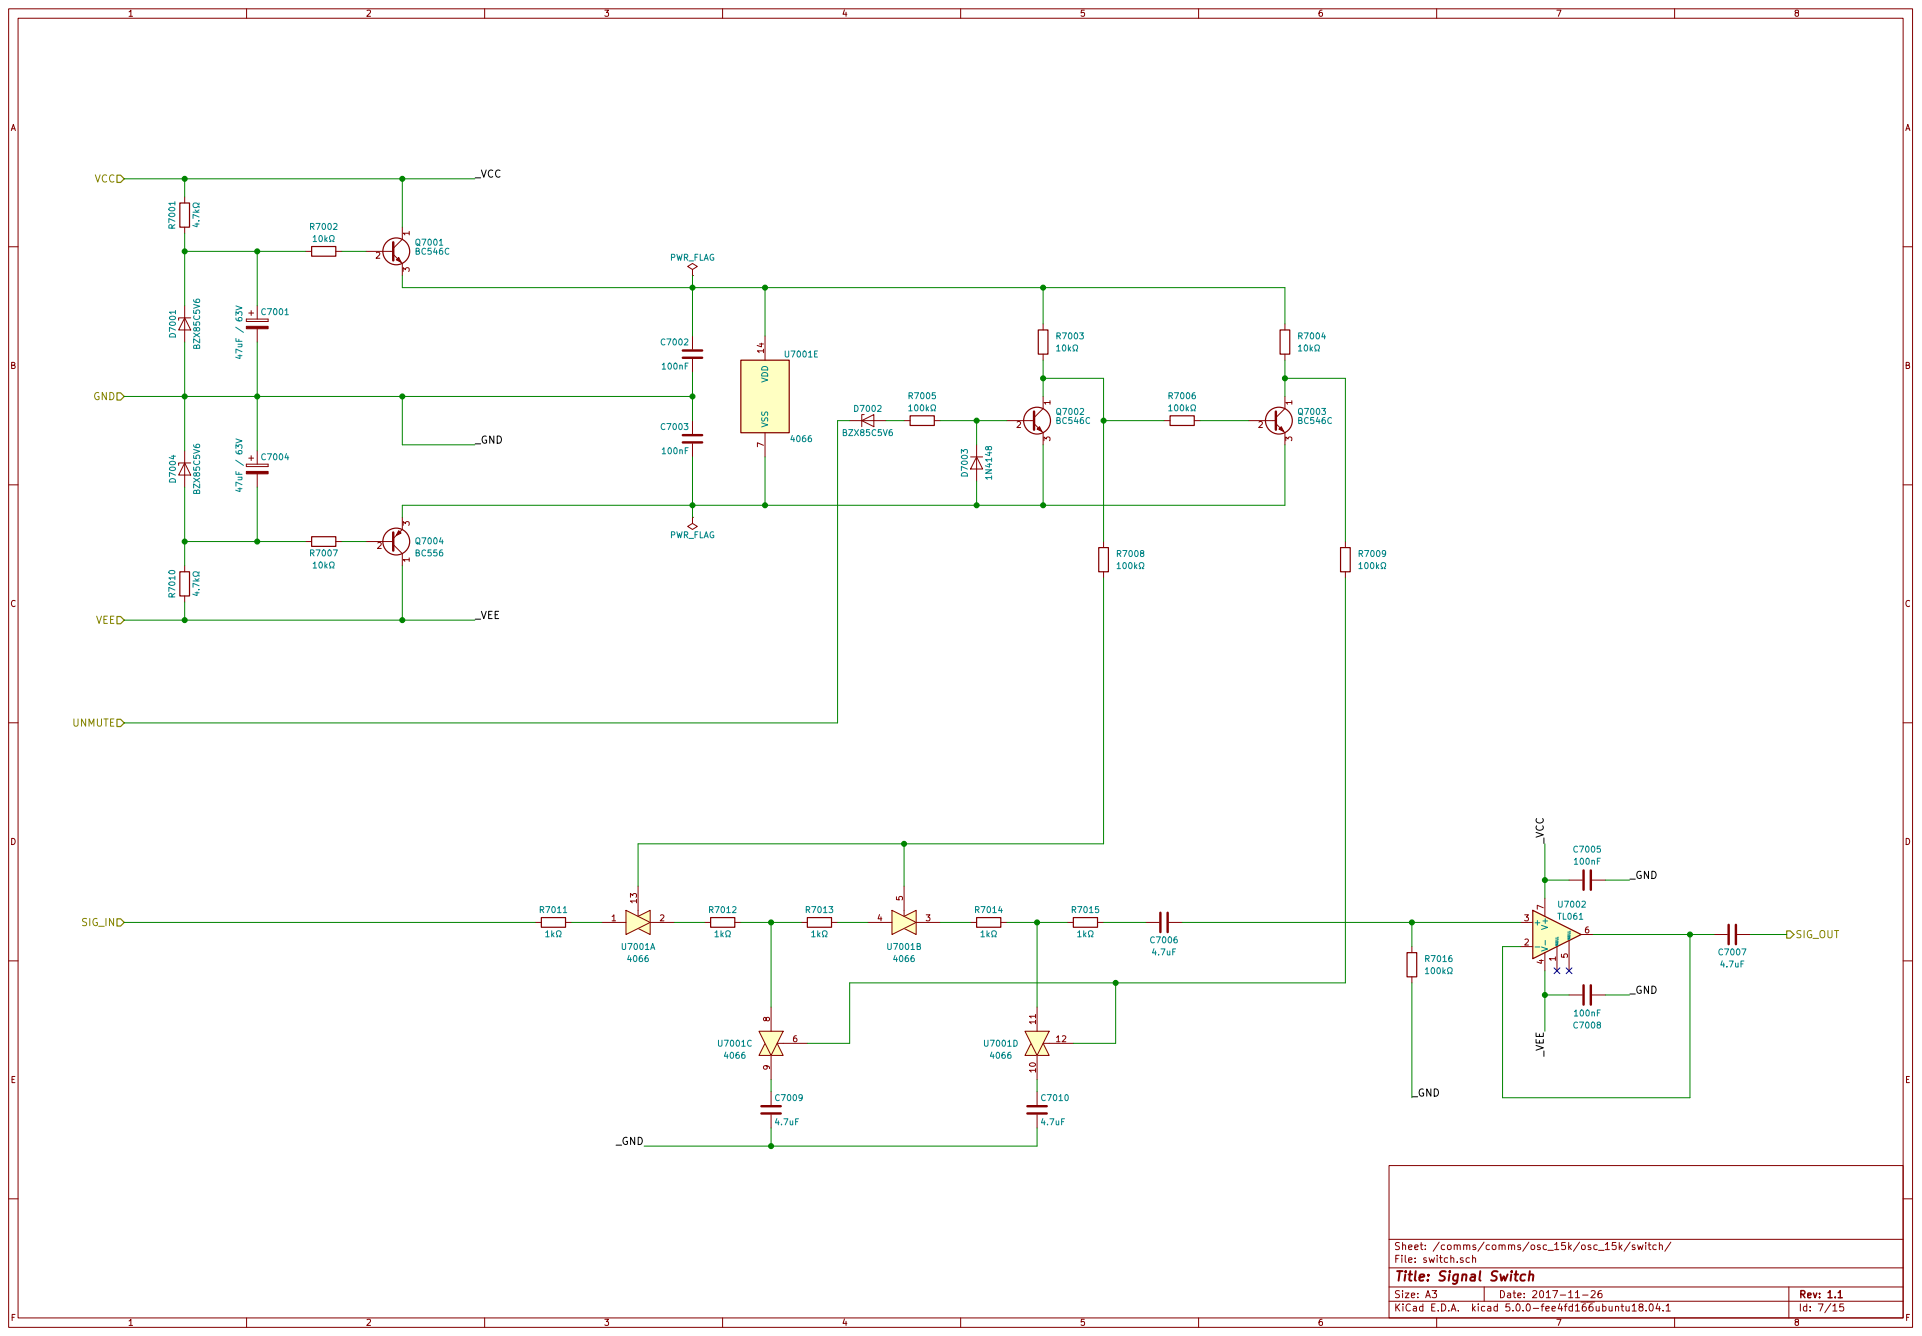
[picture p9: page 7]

File: switch.sch Sheet: /comms/comms/osc_15k/osc_15k/switch/
Id: 7/15 Title: Signal Switch

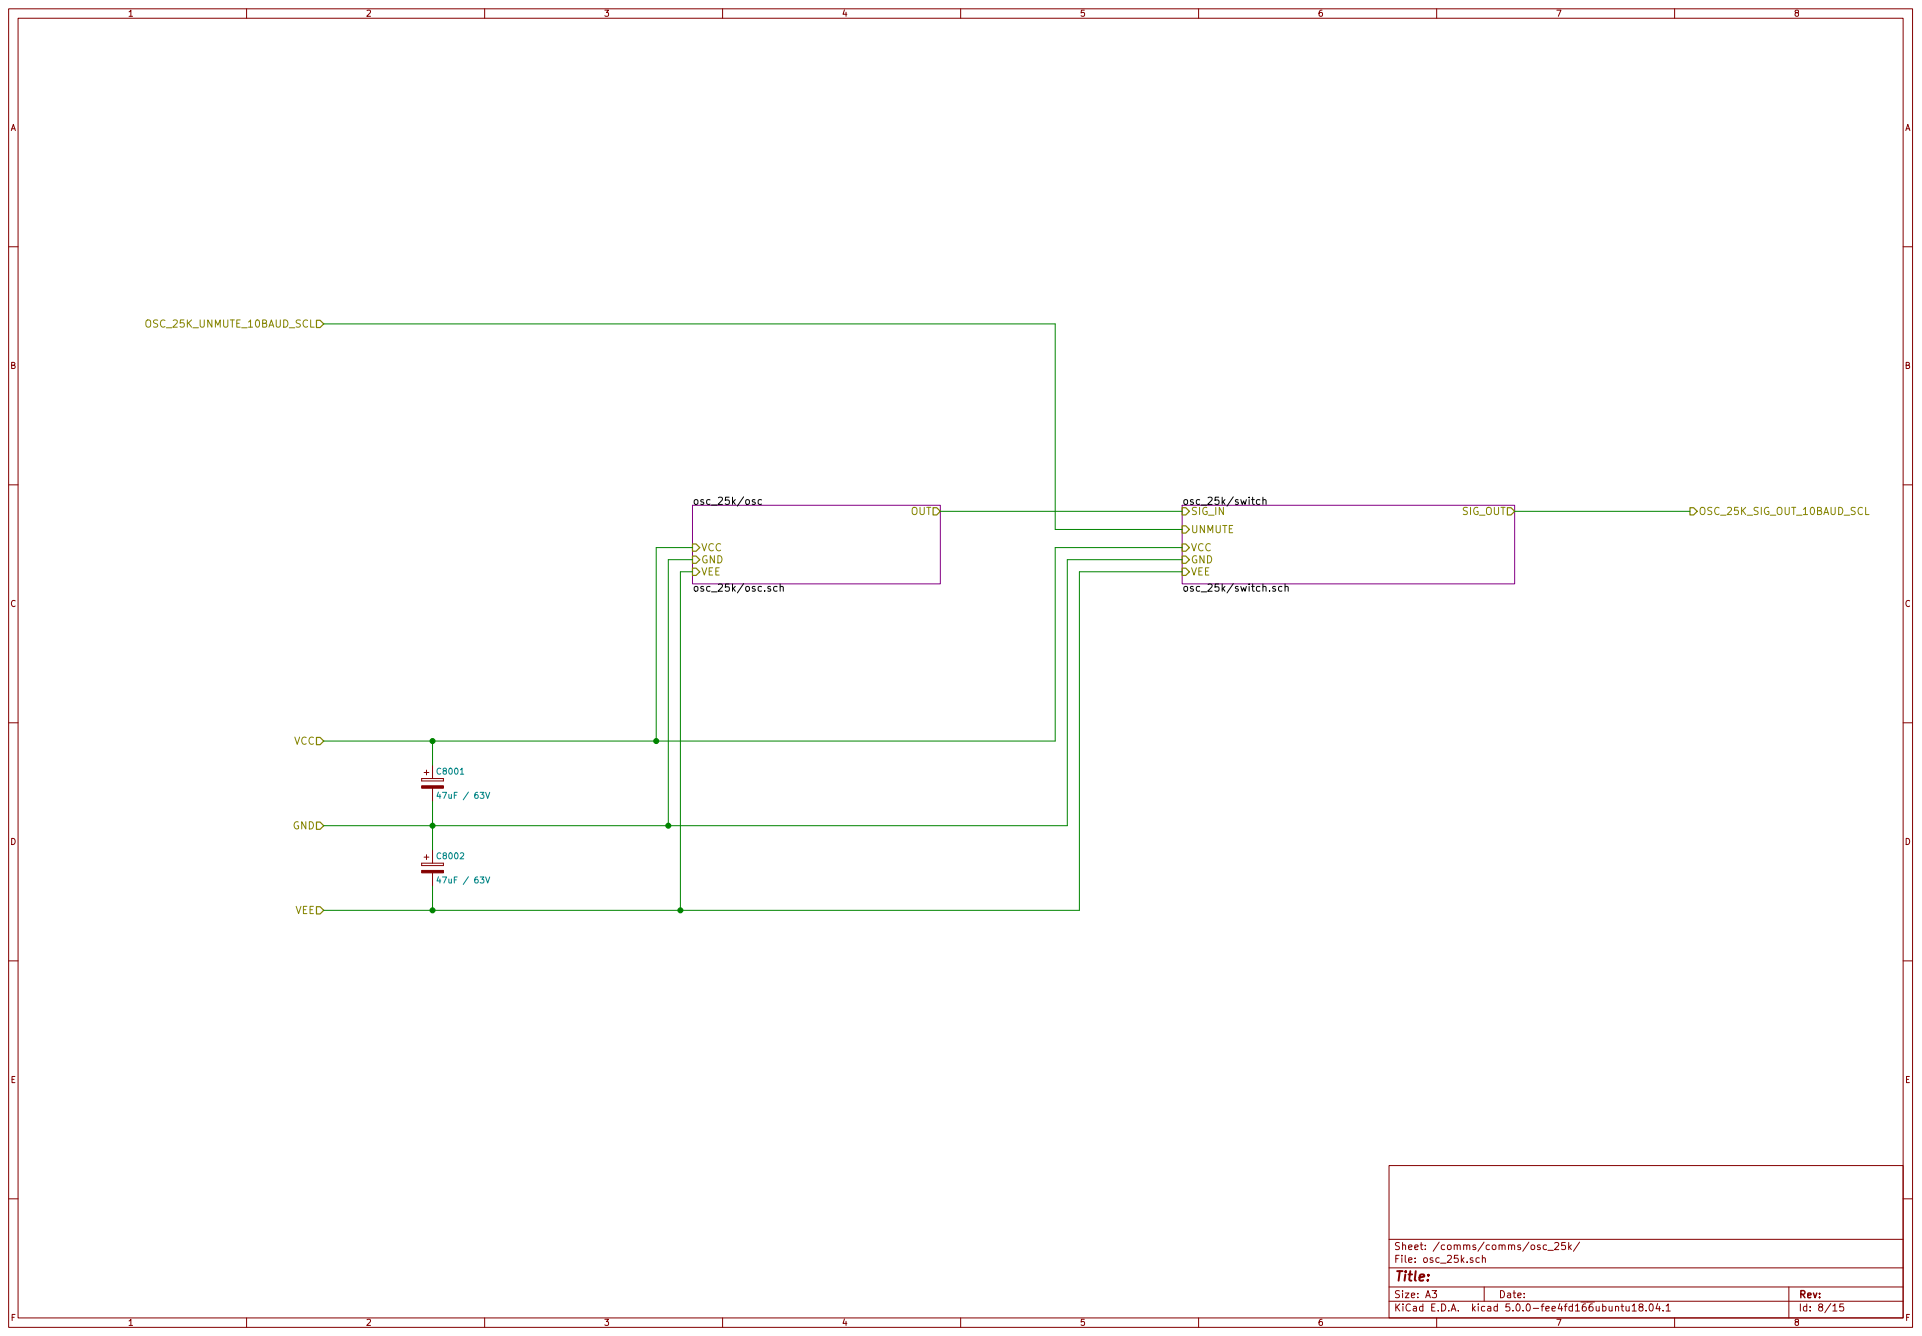
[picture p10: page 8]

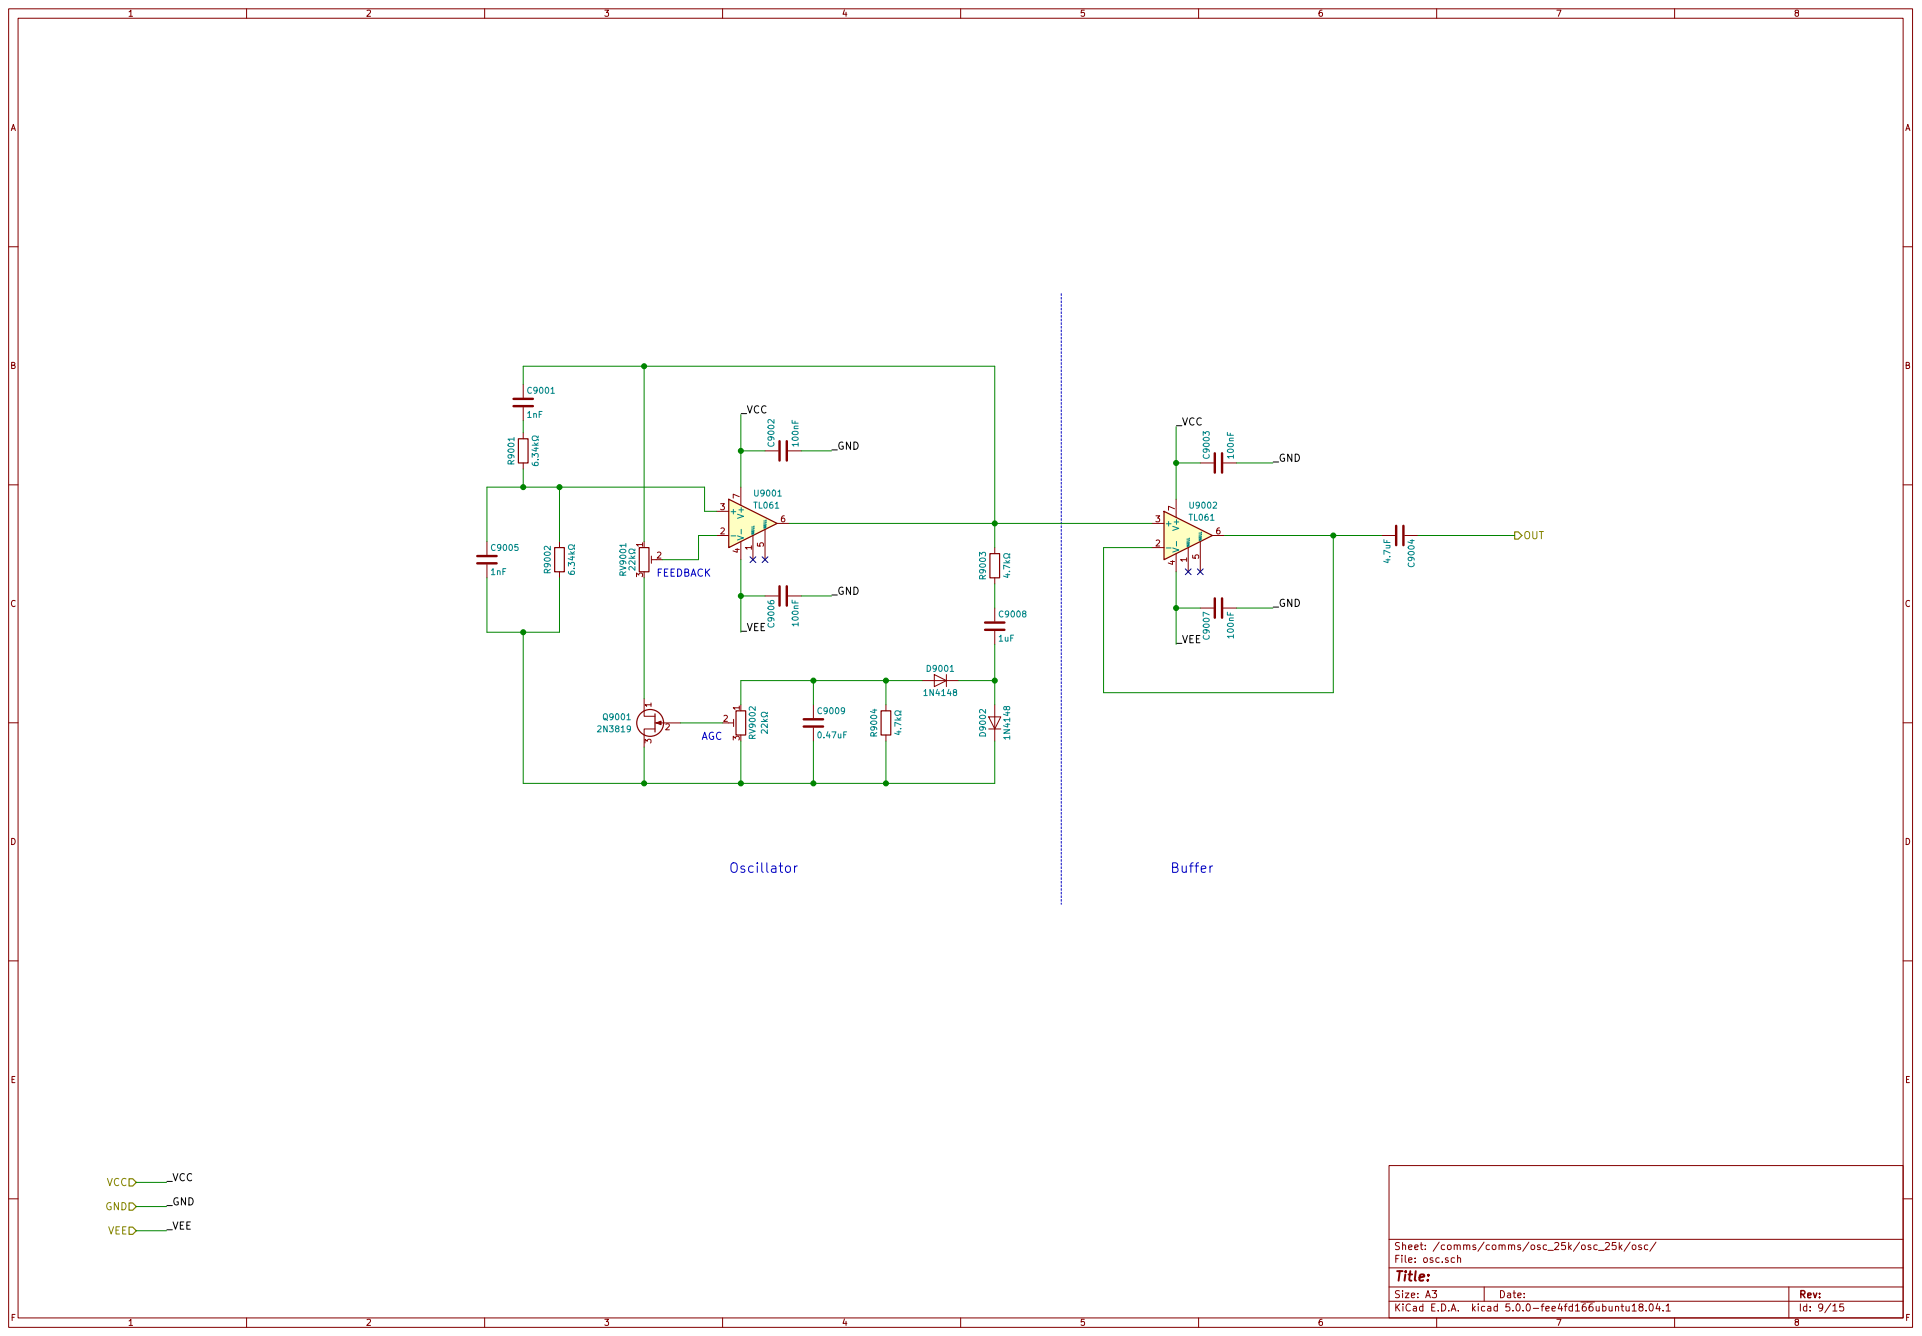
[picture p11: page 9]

7U9001 TL061 NULL 1
Id: 9/15 Title: File: osc.sch Sheet: /comms/comms/osc_25k/osc_25k/osc/ NULL 1

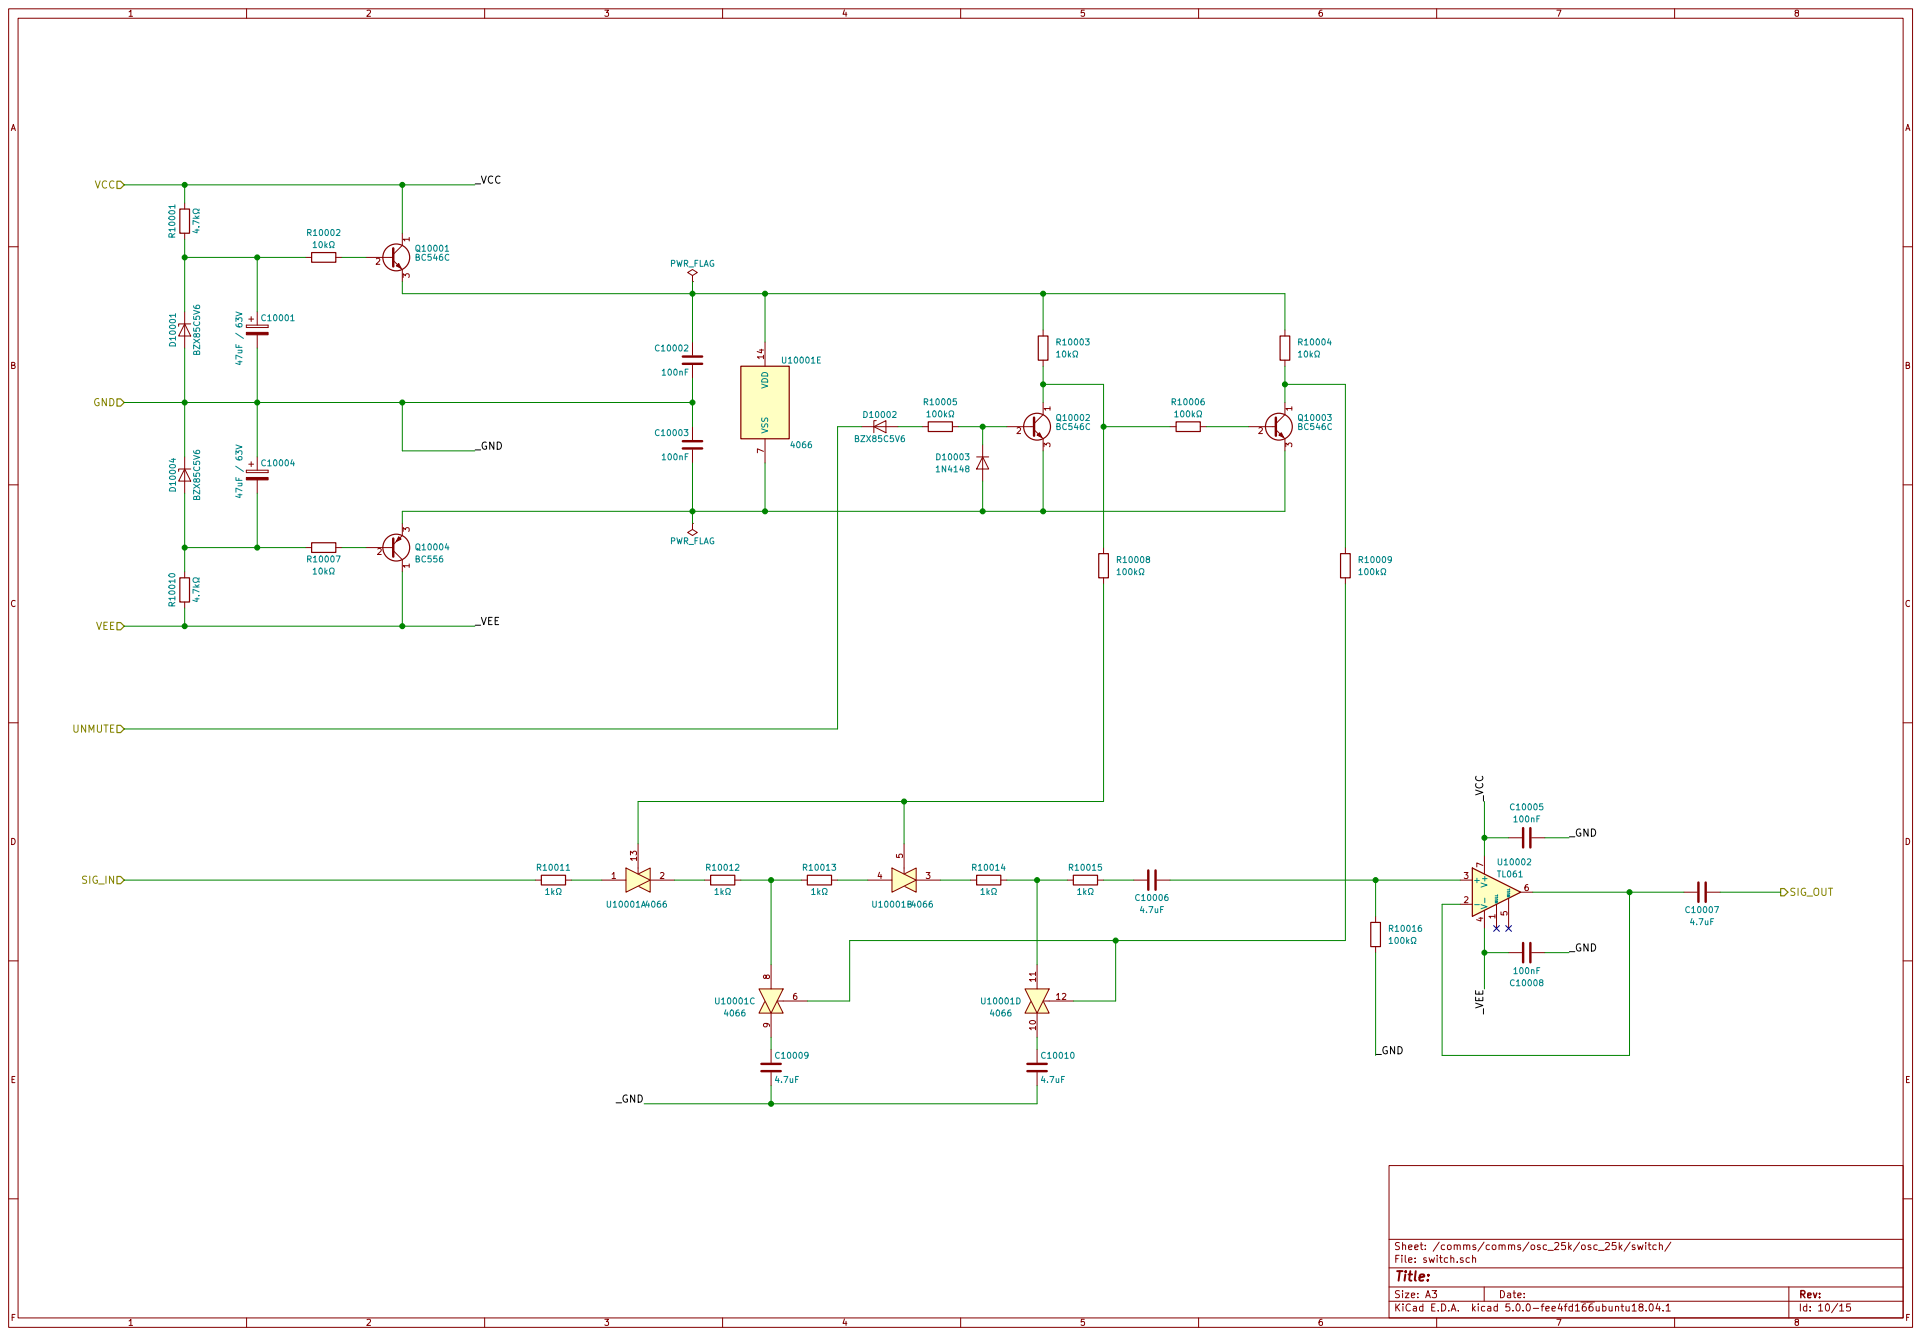
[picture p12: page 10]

Id: 10/15 Title: File: switch.sch Sheet: /comms/comms/osc_25k/osc_25k/switch/

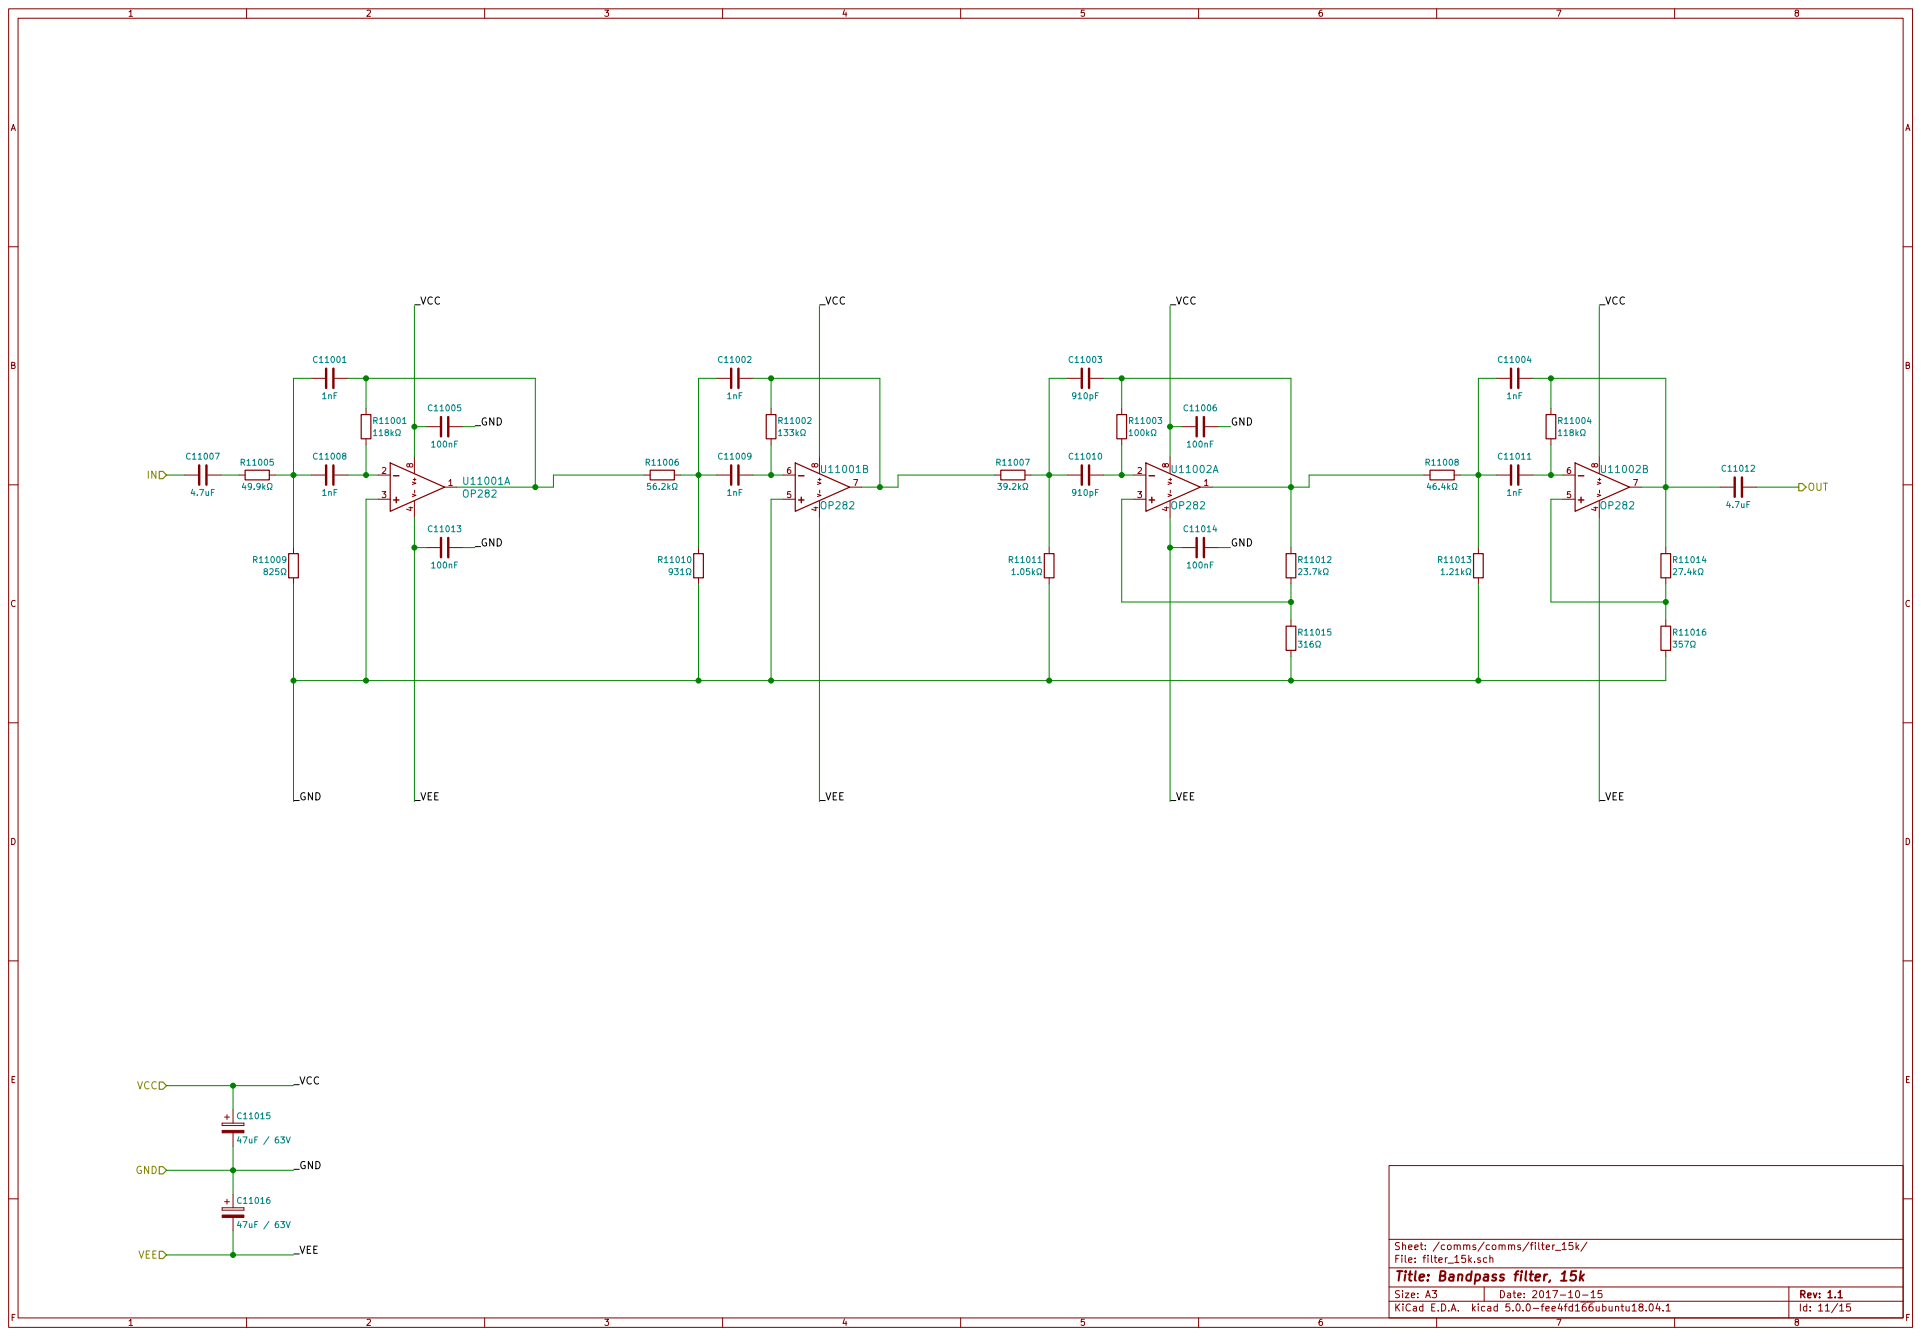
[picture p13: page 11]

Sheet: /comms/comms/filter_15k/
File: filter_15k.sch
Id: 11/15 Title: Bandpass filter, 15k

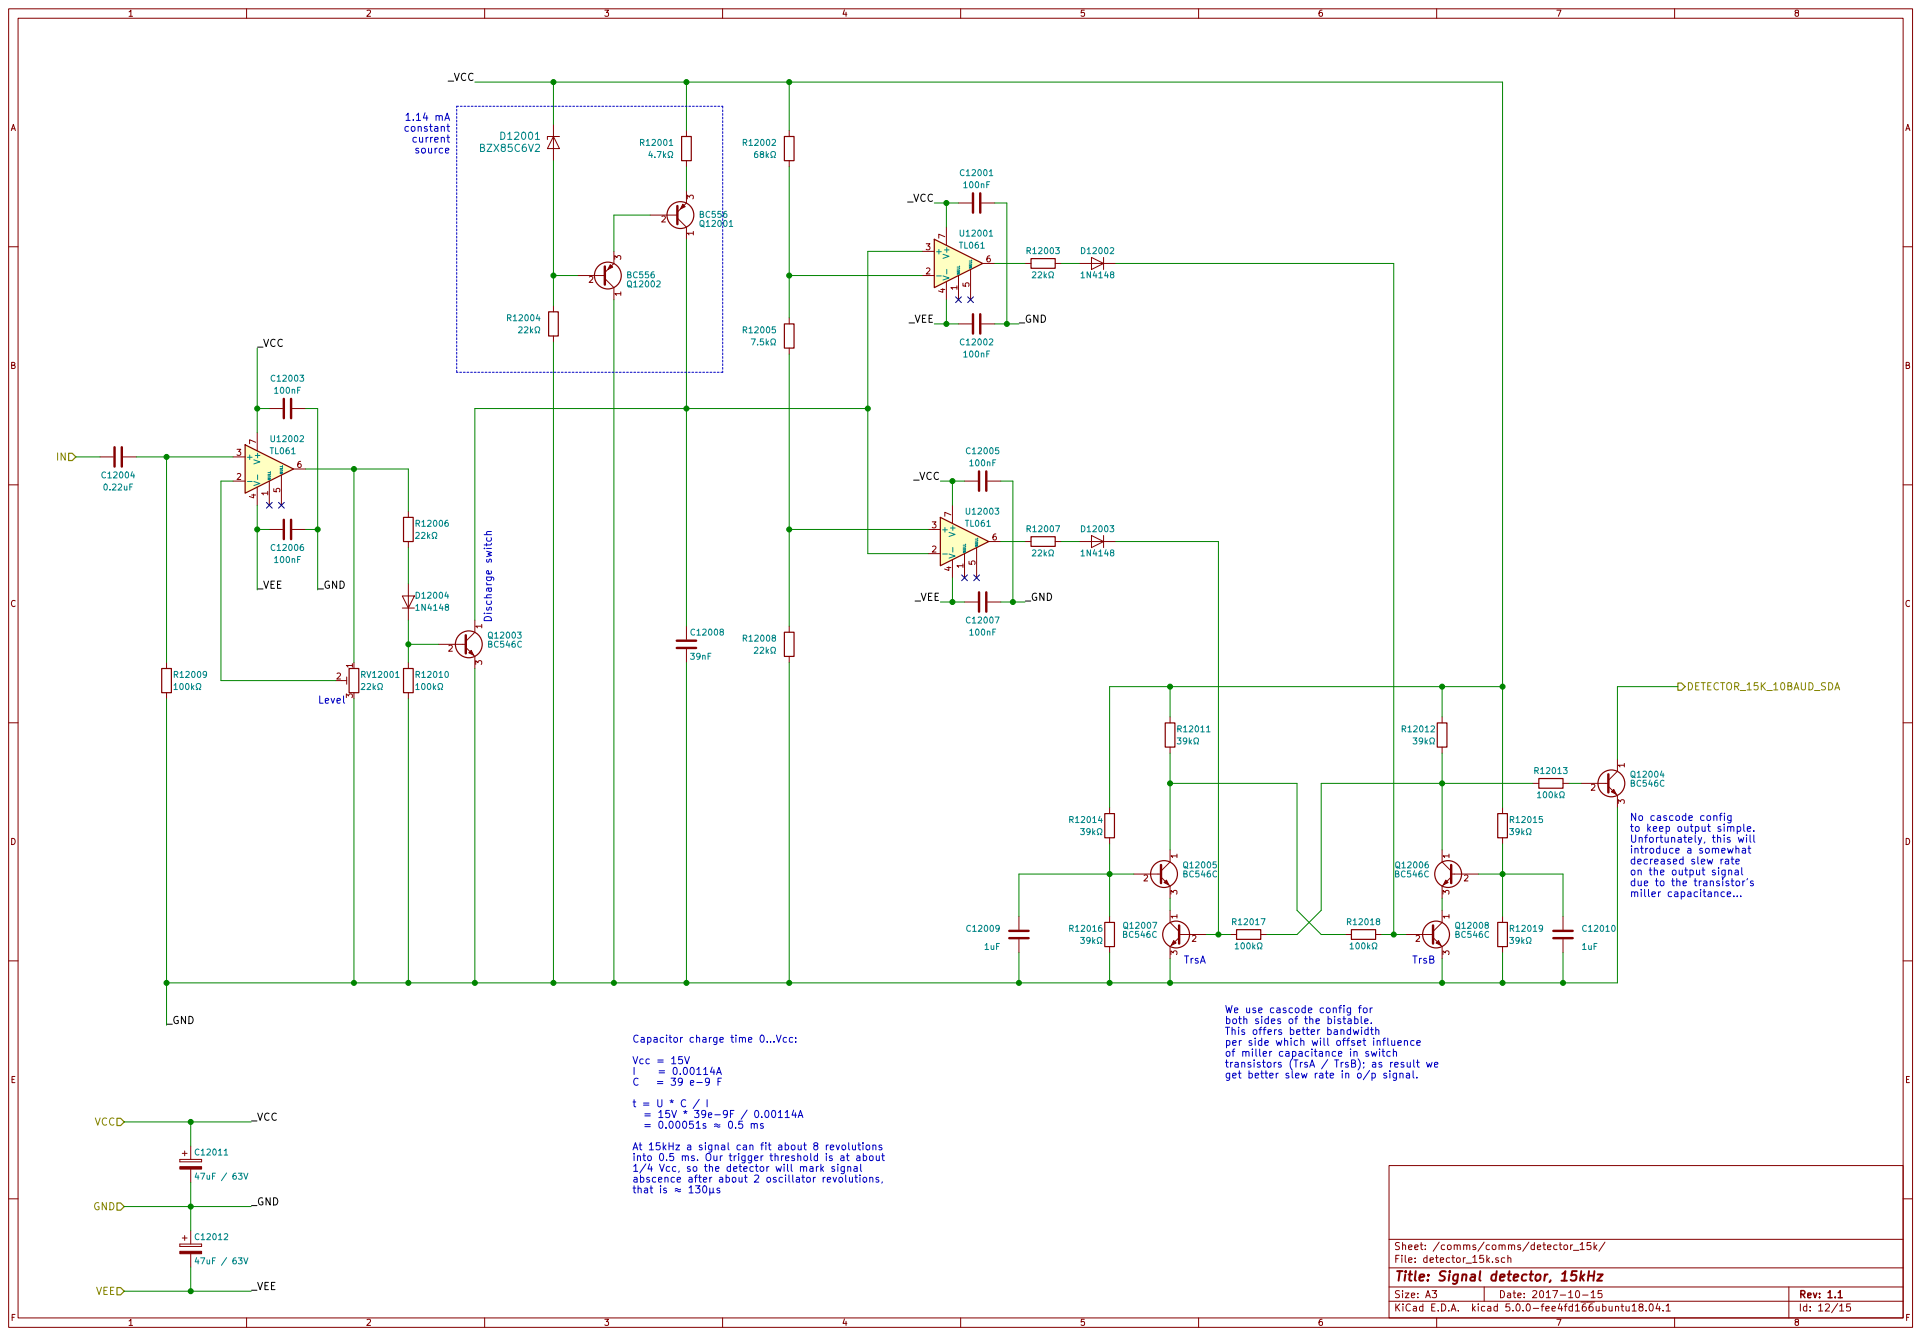
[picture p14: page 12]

3 Q12004 BC546C We use cascode config for both sides of the bistable. This offers better bandwidth per side which will offset influence

to keep output simple.
Unfortunately, this will
introduce a somewhat decreased slew rate

on the output signal due to the transistor's miller capacitance... C12009

get better slew rate in o/p signal. TrsA

Capacitor charge time 0...Vcc: Vcc = 15V

of miller capacitance in switch
transistors (TrsA / TrsB); as result we

= 0.00051s 0.5 ms At 15kHz a signal can fit about 8 revolutions

into 0.5 ms. Our trigger threshold is at about
1/4 Vcc, so the detector will mark signal
abscence after about 2 oscillator revolutions,

File: detector_15k.sch
Id: 12/15 Title: Signal detector, 15kHz


Part of the
surge protection
scheme. Part of the

File: barrier.sch Sheet: /comms/comms/barrier/
Id: 13/15 Title: Transformer Barrier module


10Baud bus WRITE_ENABLE
LO: CPU Receives serial data

Notes:
* The communication with the periphery implements
ideas from the I2C bus design with the addon that we
encode the logic levels with AC signals between
controller and peripherals. For the clock we use a
25kHz signal, for the data we use a 15kHz signal.
Signal abscent = logic 0, Signal present = logic 1
* The design is geared at EMC robustness, i.e. we
employ surge protection between controller
and periphery. Equipment operates in an area
with thunderstorms and near lightning strikes.
* As a trade-off, comms between controller and
periphery can only handle very low data rates.
It's no problem in this application as we
are handling very small amounts of data (a few bytes
per transferral) when receiving and sending data from / to
the peripherals.
* Serial clock is unidirectional as the clock is generated
by the controller with all peripheral devices listening.
* Serial data is bidirectional as the CPU both receives
and transmits data from / to the periphery devices.
* DETECTOR_15K_10BAUD_SDA is connected to an
open-collector output. It seemed best to put the

* WR_EN low (about 0V)
* TrsA open, TrsB open, TrsC closed.
* OSC_15K_UNMUTE_10BAUD_SDA pulled to GND (0V),
i.e. 15kHz oscillator will be muted.
* CPU_10BAUD_SDA follows A follows B follows DETECTOR_15K_10BAUD_SDA.
* WR_EN high (about 5V)
* TrsA closed, TrsB closed, TrsC open.
* DA will be either closed when A is on GND potential
or reverse polarized when A is on V_LOGIC potential,
i.e. B and A will be isolated from each other.
* DETECTOR_15K_10BAUD_SDA pulled to GND (0V)
i.e. 15kHz detector remains silent.
* OSC_15K_UNMUTE_10BAUD_SDA follows A follows CPU_10BAUD_SDA.
* Legend
* Trs... open: Transistor, CE, not conducting

Id: 14/15 Title: File: router.sch Sheet: /comms_router/ Router: 10Baud bus I/O

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

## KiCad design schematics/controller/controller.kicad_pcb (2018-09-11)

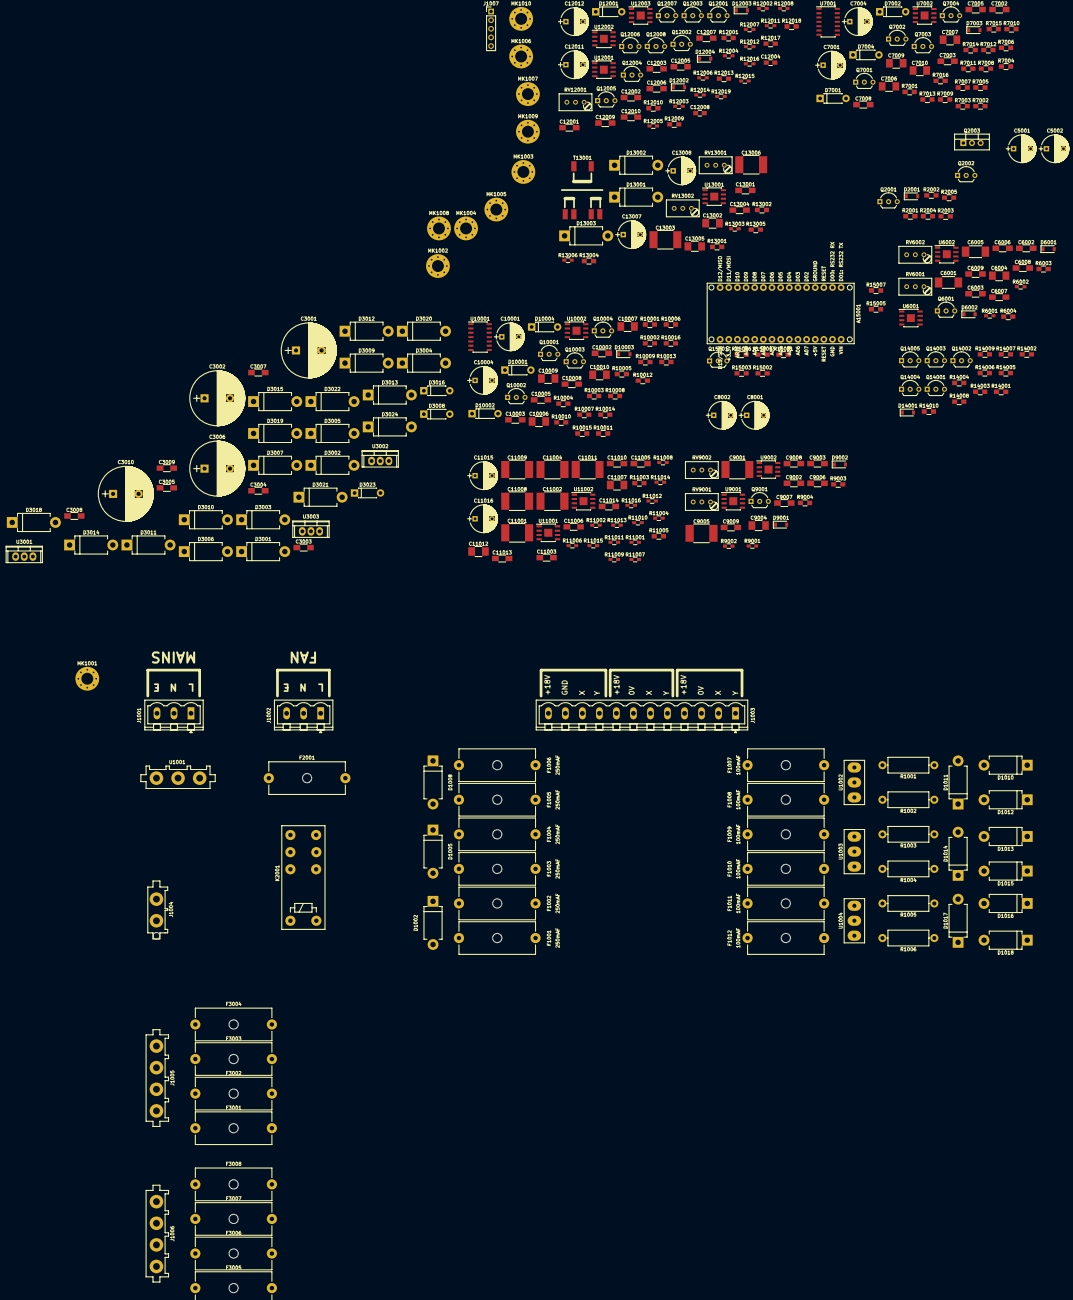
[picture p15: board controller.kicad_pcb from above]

Board: 2 copper layers, 349 parts (0 on the bottom side), 195 nets, no tracks yet.

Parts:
A15001: Arduino_Nano_v3.x; arduino-nano_3.x
C3001: 1000uF/63V; CP_Radial_D16.0mm_P7.50mm
C3002, C3006, C3010: 470uF/63V; CP_Radial_D16.0mm_P7.50mm
C3003, C3007, C3008, C6002, C6003, C6006, C6007, C7002, C7003, C7005, C7008, C9002, C9003, C9006, C9007, C10002, C10003, C10005, C10008, C11005, C11006, C11013, C11014, C12001, C12002, C12003, C12005, C12006, C12007, C13001, C13004: 100nF; C_1206_HandSoldering
C3004, C3005, C3009, C6008, C9008, C12009, C12010: 1uF; C_1206_HandSoldering
C5001, C5002, C7001, C7004, C8001, C8002, C10001, C10004, C11015, C11016, C12011, C12012, C13007, C13008: 47uF / 63V; CP_Radial_D8.0mm_P5.00mm
C6001, C6005: 2.4nF; C_1812_HandSoldering
C6004, C7006, C7007, C7009, C7010, C9004, C10006, C10007, C10009, C10010, C11007, C11012, C13002, C13005: 4.7uF; C_1210_HandSoldering
C6009, C9009: 0.47uF; C_1206_HandSoldering
C9001, C9005, C11001, C11002, C11004, C11008, C11009, C11011: 1nF; C_2220_HandSoldering
C11003, C11010: 910pF; C_1206_HandSoldering
C12004: 0.22uF; C_0805_HandSoldering
C12008: 39nF; C_0805_HandSoldering
C13003, C13006: 4.7nF; C_2220_HandSoldering
D1002, D1005, D1008: 1.5KE33CA; D_DO-201AD_P12.70mm_Horizontal
D1010, D1011, D1012, D1013, D1014, D1015, D1016, D1017, D1018: 1.5KE30CA; D_DO-201AD_P12.70mm_Horizontal
D2001, D6001, D6002, D7003, D9001, D9002, D10003, D12002, D12003, D12004, D14001: 1N4148; D_SOD-123
D3001, D3004, D3007, D3009, D3012, D3015, D3020, D3024: 1.5KE36CA; D_DO-201AD_P12.70mm_Horizontal
D3002, D3003, D3005, D3006, D3010, D3011, D3013, D3014, D3018, D3019, D3021, D3022: 1N5404; D_DO-201AD_P12.70mm_Horizontal
D3008, D3016, D3023: 1N4007; D_DO-41_SOD81_P7.62mm_Horizontal
D7001, D7002, D7004, D10001, D10002, D10004: BZX85C5V6; D_DO-41_SOD81_P7.62mm_Horizontal
D12001: BZX85C6V2; D_DO-41_SOD81_P7.62mm_Horizontal
D13001, D13002, D13003: 1.5KE12CA; D_DO-201AD_P12.70mm_Horizontal
F1001, F1002, F1003, F1004, F1005, F1006: 250mAF; Fuseholder5x20_horiz_open_Schurter_0031_8201
F1007, F1008, F1009, F1010, F1011, F1012: 100mAF; Fuseholder5x20_horiz_open_Schurter_0031_8201
F2001: 6AT; Fuseholder5x20_horiz_open_Schurter_0031_8201
F3001, F3002: 2AT; Fuseholder5x20_horiz_open_Schurter_0031_8201
F3003, F3004: 1AT; Fuseholder5x20_horiz_open_Schurter_0031_8201
F3005, F3006, F3007, F3008: 1AF; Fuseholder5x20_horiz_open_Schurter_0031_8201
J1001, J1002: Screw_Terminal_01x03; PhoenixContact_MSTBVA-G_03x5.00mm_Vertical
J1003: Periphery; PhoenixContact_MSTBVA-G_12x5.00mm_Vertical
J1004: Conn_01x02_Male; TE_1969799-1
J1005, J1006: Conn_01x04_Male; TE_1969807-1
J1007: FRONTPANEL; Pin_Header_Straight_1x05_Pitch2.54mm
K2001: TE RT424024 (24VDC@1.44kOhm, DPDT, 250VAC, 8A); Relay_DPDT_Schrack-RT2-FormC_RM5.04mm
MK1001, MK1002, MK1003, MK1004, MK1005, MK1006, MK1007, MK1008, MK1009, MK1010: 3.5; MountingHole_3.5mm_Pad_Via
Q2001, Q7004, Q10004, Q12001, Q12002: BC556; TO-92_Inline_Wide
Q2002, Q7001, Q7002, Q7003, Q10001, Q10002, Q10003, Q12003, Q12004, Q12005, Q12006, Q12007, Q12008, Q14001, Q14002, Q14003, Q14004, Q14005, Q15001: BC546C; TO-92_Inline_Wide
Q2003: BD243C; TO-220-3_Vertical
Q6001, Q9001: 2N3819; TO-92_Inline_Wide
R1001, R1002, R1003, R1004, R1005, R1006: 27Ω / 1W; R_Axial_DIN0414_L11.9mm_D4.5mm_P15.24mm_Horizontal
R2001, R2005, R7005, R7006, R7008, R7009, R7016, R10005, R10006, R10008, R10009, R10016, R11003, R12009, R12010, R12013, R12017, R12018, R13004, R13005, R14002, R14003, R14007, R14009, R14010: 100kΩ; R_0805_HandSoldering
R2002, R2003, R7002, R7003, R7004, R7007, R10002, R10003, R10004, R10007, R13001, R13002, R14001, R14004, R14005, R14006, R14008, R15001, R15002, R15003, R15004, R15005, R15006, R15007: 10kΩ; R_0805_HandSoldering
R2004, R6003, R6004, R7001, R7010, R9003, R9004, R10001, R10010, R12001: 4.7kΩ; R_0805_HandSoldering
R6001, R6002: 4.42kΩ; R_0603_HandSoldering
R7011, R7012, R7013, R7014, R7015, R10011, R10012, R10013, R10014, R10015: 1kΩ; R_0805_HandSoldering
R9001, R9002: 6.34kΩ; R_0603_HandSoldering
R11001, R11004: 118kΩ; R_0603_HandSoldering
R11002: 133kΩ; R_0603_HandSoldering
R11005: 49.9kΩ; R_0805_HandSoldering
R11006: 56.2kΩ; R_0603_HandSoldering
R11007: 39.2kΩ; R_0603_HandSoldering
R11008: 46.4kΩ; R_0603_HandSoldering
R11009: 825Ω; R_0603_HandSoldering
R11010: 931Ω; R_0603_HandSoldering
R11011: 1.05kΩ; R_0603_HandSoldering
R11012: 23.7kΩ; R_0603_HandSoldering
R11013: 1.21kΩ; R_0603_HandSoldering
R11014: 27.4kΩ; R_0603_HandSoldering
R11015: 316Ω; R_0603_HandSoldering
R11016: 357Ω; R_0603_HandSoldering
R12002: 68kΩ; R_0603_HandSoldering
R12003, R12004, R12006, R12007, R12008: 22kΩ; R_0603_HandSoldering
R12005: 7.5kΩ; R_0603_HandSoldering
R12011, R12012, R12014, R12015, R12016, R12019: 39kΩ; R_0603_HandSoldering
R13003, R13006: 220Ω; R_0603_HandSoldering
RV6001, RV6002, RV9001, RV9002, RV12001, RV13001, RV13002: 22kΩ; Potentiometer_Trimmer_Bourns_3296W
T13001: Transformer_2P_1S; TRANSFORMER_VENDOR_VACUUMSCHMELZE_T60403-K5032-X102
U1001: Module: surgeprot.mains.275.5.01; TE_1969803-1
U1002, U1003, U1004: Bourns 2026-07-C2LF; Bourns_2026-xx
U3001: L7805; TO-220
U3002: L7815; TO-220
U3003: L7915; TO-220
U6001, U6002, U7002, U9001, U9002, U10002, U12001, U12002, U12003: TL061; SOIC-8-1EP_3.9x4.9mm_Pitch1.27mm
U7001, U10001: 4066; SOIC-14_3.9x8.7mm_Pitch1.27mm
U11001, U11002, U13001: OP282; SOIC-8-1EP_3.9x4.9mm_Pitch1.27mm

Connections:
/comms/DETECTOR_15K_10BAUD_SDA: D14001.2, Q12004.1, Q14003.1, R14005.2
/comms/OSC_15K_UNMUTE_10BAUD_SDA: D7002.1, Q14004.1, R14006.1
/comms/OSC_25K_UNMUTE_10BAUD_SCL: D10002.1, Q14001.3, R14003.1
/comms/VCC: C3005.1, C5001.1, C6002.1, C6003.1, C7005.2, C8001.1, C9002.1, C9003.1, C10005.2, C11005.1, C11006.1, C11015.1, C12001.2, C12003.2, C12005.2, C12011.1, C13001.1, C13007.1, D3016.2, D12001.2, Q7001.1, Q10001.1, R7001.1, R10001.1, R12001.1, R12002.1, R12011.1, R12012.1, R12014.1, R12015.1, U3002.3, U6001.7, U6002.7, U7002.7, U9001.7, U9002.7, U10002.7, U11001.8, U11002.8, U12001.7, U12002.7, U12003.7, U13001.8
/comms/VEE: C3009.2, C5002.2, C6006.1, C6007.1, C7008.2, C8002.2, C9006.1, C9007.1, C10008.2, C11013.1, C11014.1, C11016.2, C12002.2, C12006.2, C12007.2, C12012.2, C13004.1, C13008.2, D3023.1, Q7004.1, Q10004.1, R7010.2, R10010.2, U3003.3, U6001.4, U6002.4, U7002.4, U9001.4, U9002.4, U10002.4, U11001.4, U11002.4, U12001.4, U12002.4, U12003.4, U13001.4
/comms/X: D1010.2, D1011.2, D1013.2, D1014.2, D1016.2, D1017.2, R1001.1, R1003.1, R1005.1, T13001.1
/comms/Y: D1011.1, D1012.2, D1014.1, D1015.2, D1017.1, D1018.2, R1002.1, R1004.1, R1006.1, T13001.2
/comms/comms/barrier/OSC_15K_SIG_OUT_10BAUD_SDA: C7007.1, R13001.2
/comms/comms/barrier/OSC_25K_SIG_OUT_10BAUD_SCL: C10007.1, R13002.2
/comms/comms/detector_15k/IN: C11012.2, C12004.2
/comms/comms/filter_15k/IN: C11007.1, RV13002.3, U13001.7
/comms/comms/osc_15k/osc_15k/osc/OUT: C6004.1, R7011.2
/comms/comms/osc_25k/osc_25k/osc/OUT: C9004.1, R10011.2
/comms_router/CPU_10BAUD_SCL: A15001.6, R14001.2, R15005.2
/comms_router/CPU_10BAUD_SDA: A15001.5, R14004.2, R15006.2
/comms_router/CPU_10BAUD_WR_EN: A15001.7, R14008.2, R15004.2
/comms_router/V_LOGIC: A15001.27, C3004.1, D3008.2, J1007.4, Q14001.1, Q14002.1, R14005.1, R14007.1, R15001.1, R15002.1, R15003.1, R15004.1, R15005.1, R15006.1, U3001.3
/cpu/CPU_HIBAUD_SCL: A15001.24, J1007.1, R15001.2
/cpu/CPU_HIBAUD_SDA: A15001.23, J1007.2, R15002.2
/cpu/FAN_ON: A15001.8, R2003.1, R15003.2
/cpu/RESET: J1007.3, R15007.1
/fan-switch/L: F2001.1, J1001.1, U1001.1
/fan-switch/LFAN: J1002.1, K2001.24
/fan-switch/N: J1001.2, J1004.1, K2001.11, U1001.2
/fan-switch/NFAN: J1002.2, K2001.14
/psu/TR01-1: F3001.1, J1005.1
/psu/TR01-2: F3002.1, J1005.2
/psu/TR01-3: F3003.1, J1005.3
/psu/TR01-4: F3004.1, J1005.4
/psu/TR02-1: F3005.1, J1006.1
/psu/TR02-2: F3006.1, J1006.2
/psu/TR02-3: F3007.1, J1006.3
/psu/TR02-4: F3008.1, J1006.4
/psu/V_DCDC_+18: C3001.1, D1002.2, D1005.2, D1008.2, D2001.1, D3003.1, D3006.1, F1001.1, F1003.1, F1005.1, K2001.A2, Q2001.3, R2001.1
Earth: A15001.4, A15001.29, C3001.2, C3002.2, C3003.2, C3004.2, C3005.2, C3006.2, C3007.2, C3008.1, C3009.1, C3010.1, C5001.2, C5002.1, C6002.2, C6003.2, C6006.2, C6007.2, C7001.2, C7002.2, C7003.1, C7004.1, C7005.1, C7008.1, C7009.2, C7010.2, C8001.2, C8002.1, C9002.2, C9003.2, C9006.2, C9007.2, C10001.2, C10002.2, C10003.1, C10004.1, C10005.1, C10008.1, C10009.2, C10010.2, C11005.2, C11006.2, C11013.2, C11014.2, C11015.2, C11016.1, C12001.1, C12002.1, C12003.1, C12005.1, C12006.1, C12007.1, C12008.2, C12009.2, C12010.2, C12011.2, C12012.1, C13001.2, C13003.1, C13004.2, C13006.1, C13007.2, C13008.1, D1002.1, D1005.1, D1008.1, D1010.1, D1012.1, D1013.1, D1015.1, D1016.1, D1018.1, D3001.1, D3002.2, D3005.2, D3007.2, D3009.1, D3010.2, D3013.2, D3015.2, D3020.1, D3024.2, D7001.2, D7004.1, D10001.2, D10004.1, D13001.2, D13003.1, F1002.1, F1004.1, F1006.1, F3006.2, F3007.2, J1001.3, J1002.3, J1007.5, MK1001.1, MK1002.1, MK1003.1, MK1004.1, MK1005.1, MK1006.1, MK1007.1, MK1008.1, MK1009.1, MK1010.1, Q2002.3, Q2003.3, Q12002.1, Q12003.3, Q12004.3, Q12007.3, Q12008.3, Q14003.3, Q14004.3, Q14005.3, Q15001.3, R2005.2, R7016.2, R10016.2, R11009.2, R11010.2, R11011.2, R11013.2, R11015.2, R11016.2, R12004.2, R12008.2, R12009.2, R12010.2, R12016.2, R12019.2, R13004.1, R13005.2, R14002.2, R14003.2, R14009.2, R14010.2, RV12001.3, RV13001.3, RV13002.1, T13001.4, T13001.5, U1002.2, U1003.2, U1004.2, U3001.2, U3002.2, U3003.1, U11001.3, U11001.5
unnamed: A15001.3, A15001.28, Q15001.1
unnamed: C3002.1, C3003.1, D3008.1, D3011.1, D3014.1, U3001.1
unnamed: C3006.1, C3007.1, D3016.1, D3019.1, D3022.1, U3002.1
unnamed: C3008.2, C3010.2, D3018.2, D3021.2, D3023.2, U3003.2
unnamed: C6001.1, R6003.1, RV6001.1, U6001.6, U6002.3
unnamed: C6001.2, R6001.1
unnamed: C6004.2, U6002.2, U6002.6
unnamed: C6005.1, R6001.2, R6002.1, U6001.3
unnamed: C6005.2, C6009.2, D6002.1, Q6001.3, R6002.2, R6004.2, RV6002.3
unnamed: C6008.1, R6003.2
unnamed: C6008.2, D6001.1, D6002.2
unnamed: C6009.1, D6001.2, R6004.1, RV6002.1
unnamed: C7001.1, D7001.1, R7001.2, R7002.2
unnamed: C7002.1, Q7001.3, R7003.1, R7004.1, U7001.14
unnamed: C7003.2, D7003.2, Q7002.3, Q7003.3, Q7004.3, U7001.7
unnamed: C7004.2, D7004.2, R7007.2, R7010.1
unnamed: C7006.1, R7016.1, U7002.3
unnamed: C7006.2, R7015.1
unnamed: C7007.2, U7002.2, U7002.6
unnamed: C7009.1, U7001.9
unnamed: C7010.1, U7001.10
unnamed: C9001.1, R9003.1, RV9001.1, U9001.6, U9002.3
unnamed: C9001.2, R9001.1
unnamed: C9004.2, U9002.2, U9002.6
unnamed: C9005.1, R9001.2, R9002.1, U9001.3
unnamed: C9005.2, C9009.2, D9002.1, Q9001.3, R9002.2, R9004.2, RV9002.3
unnamed: C9008.1, R9003.2
unnamed: C9008.2, D9001.1, D9002.2
unnamed: C9009.1, D9001.2, R9004.1, RV9002.1
unnamed: C10001.1, D10001.1, R10001.2, R10002.2
unnamed: C10002.1, Q10001.3, R10003.1, R10004.1, U10001.14
unnamed: C10003.2, D10003.2, Q10002.3, Q10003.3, Q10004.3, U10001.7
unnamed: C10004.2, D10004.2, R10007.2, R10010.1
unnamed: C10006.1, R10016.1, U10002.3
unnamed: C10006.2, R10015.1
unnamed: C10007.2, U10002.2, U10002.6
unnamed: C10009.1, U10001.9
unnamed: C10010.1, U10001.10
unnamed: C11001.1, C11008.1, R11005.2, R11009.1
unnamed: C11001.2, R11001.1, R11006.1, U11001.1
unnamed: C11002.1, C11009.1, R11006.2, R11010.1
unnamed: C11002.2, R11002.1, R11007.1, U11001.7
unnamed: C11003.1, C11010.1, R11007.2, R11011.1
unnamed: C11003.2, R11003.1, R11008.1, R11012.1, U11002.1
unnamed: C11004.1, C11011.1, R11008.2, R11013.1
unnamed: C11004.2, C11012.1, R11004.1, R11014.1, U11002.7
unnamed: C11007.2, R11005.1
unnamed: C11008.2, R11001.2, U11001.2
unnamed: C11009.2, R11002.2, U11001.6
unnamed: C11010.2, R11003.2, U11002.2
unnamed: C11011.2, R11004.2, U11002.6
unnamed: C12004.1, R12009.1, U12002.3
unnamed: C12008.1, Q12001.1, Q12003.1, U12001.3, U12003.2
unnamed: C12009.1, Q12005.2, R12014.2, R12016.1
unnamed: C12010.1, Q12006.2, R12015.2, R12019.1
unnamed: C13002.1, C13003.2, R13003.2
unnamed: C13002.2, RV13001.1, U13001.1
unnamed: C13005.1, C13006.2, R13006.1
unnamed: C13005.2, R13005.1, U13001.5
unnamed: D2001.2, K2001.A1, Q2003.2
unnamed: D3001.2, D3002.1, D3003.2, D3004.2, F3001.2
unnamed: D3004.1, D3005.1, D3006.2, D3007.1, F3002.2
unnamed: D3009.2, D3010.1, D3011.2, D3012.2, F3003.2
unnamed: D3012.1, D3013.1, D3014.2, D3015.1, F3004.2
unnamed: D3018.1, D3019.2, D3020.2, F3005.2
unnamed: D3021.1, D3022.2, D3024.1, F3008.2
unnamed: D7002.2, R7005.2
unnamed: D7003.1, Q7002.2, R7005.1
unnamed: D10002.2, R10005.2
unnamed: D10003.1, Q10002.2, R10005.1
unnamed: D12001.1, Q12002.2, R12004.1
unnamed: D12002.1, Q12008.2, R12018.2
unnamed: D12002.2, R12003.2
unnamed: D12003.1, Q12007.2, R12017.1
unnamed: D12003.2, R12007.2
unnamed: D12004.1, Q12003.2, R12010.1
unnamed: D12004.2, R12006.2
unnamed: D13001.1, D13002.1, R13003.1, T13001.3
unnamed: D13002.2, D13003.2, R13006.2, T13001.6
unnamed: D14001.1, Q14002.2, R14004.1
unnamed: F1001.2, J1003.1
unnamed: F1002.2, J1003.2
unnamed: F1003.2, J1003.5
unnamed: F1004.2, J1003.6
unnamed: F1005.2, J1003.9
unnamed: F1006.2, J1003.10
unnamed: F1007.1, R1001.2, U1002.1
unnamed: F1007.2, J1003.3
unnamed: F1008.1, R1002.2, U1002.3
unnamed: F1008.2, J1003.4
unnamed: F1009.1, R1003.2, U1003.1
unnamed: F1009.2, J1003.7
unnamed: F1010.1, R1004.2, U1003.3
unnamed: F1010.2, J1003.8
unnamed: F1011.1, R1005.2, U1004.1
unnamed: F1011.2, J1003.11
unnamed: F1012.1, R1006.2, U1004.3
unnamed: F1012.2, J1003.12
unnamed: F2001.2, K2001.21
unnamed: J1004.2, U1001.3
unnamed: Q2001.1, R2004.1, R2005.1
unnamed: Q2001.2, R2002.2
unnamed: Q2002.1, R2001.2, R2002.1
unnamed: Q2002.2, R2003.2
unnamed: Q2003.1, R2004.2
unnamed: Q6001.1, RV6001.3
unnamed: Q6001.2, RV6002.2
unnamed: Q7001.2, R7002.1
unnamed: Q7002.1, R7003.2, R7006.2, R7008.1
unnamed: Q7003.1, R7004.2, R7009.1
unnamed: Q7003.2, R7006.1
unnamed: Q7004.2, R7007.1
unnamed: Q9001.1, RV9001.3
unnamed: Q9001.2, RV9002.2
unnamed: Q10001.2, R10002.1
unnamed: Q10002.1, R10003.2, R10006.2, R10008.1
unnamed: Q10003.1, R10004.2, R10009.1
unnamed: Q10003.2, R10006.1
unnamed: Q10004.2, R10007.1
unnamed: Q12001.2, Q12002.3
unnamed: Q12001.3, R12001.2
unnamed: Q12004.2, R12013.2
unnamed: Q12005.1, R12011.2, R12018.1
unnamed: Q12005.3, Q12007.1
unnamed: Q12006.1, R12012.2, R12013.1, R12017.2
unnamed: Q12006.3, Q12008.1
unnamed: Q14001.2, R14001.1, R14002.1
unnamed: Q14002.3, R14006.2, R14010.1
unnamed: Q14003.2, Q14005.2, R14008.1, R14009.1
unnamed: Q14004.2, Q14005.1, R14007.2
unnamed: Q15001.2, R15007.2
unnamed: R7008.2, U7001.5, U7001.13
unnamed: R7009.2, U7001.6, U7001.12
unnamed: R7011.1, U7001.1
unnamed: R7012.1, R7013.2, U7001.8
unnamed: R7012.2, U7001.2
unnamed: R7013.1, U7001.4
unnamed: R7014.1, R7015.2, U7001.11
unnamed: R7014.2, U7001.3
unnamed: R10008.2, U10001.5, U10001.13
unnamed: R10009.2, U10001.6, U10001.12
unnamed: R10011.1, U10001.1
unnamed: R10012.1, R10013.2, U10001.8
unnamed: R10012.2, U10001.2
unnamed: R10013.1, U10001.4
unnamed: R10014.1, R10015.2, U10001.11
unnamed: R10014.2, U10001.3
unnamed: R11012.2, R11015.1, U11002.3
unnamed: R11014.2, R11016.1, U11002.5
unnamed: R12002.2, R12005.1, U12001.2
unnamed: R12003.1, U12001.6
unnamed: R12005.2, R12008.1, U12003.3
unnamed: R12006.1, RV12001.1, U12002.6
unnamed: R12007.1, U12003.6
unnamed: R13001.1, R13002.1, R13004.2, U13001.3
unnamed: RV6001.2, U6001.2
unnamed: RV9001.2, U9001.2
unnamed: RV12001.2, U12002.2
unnamed: RV13001.2, U13001.2
unnamed: RV13002.2, U13001.6

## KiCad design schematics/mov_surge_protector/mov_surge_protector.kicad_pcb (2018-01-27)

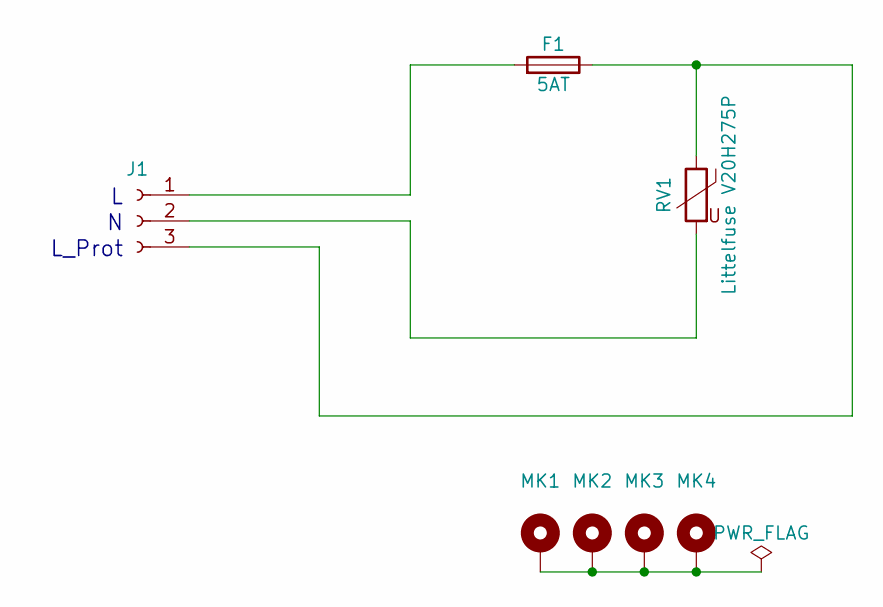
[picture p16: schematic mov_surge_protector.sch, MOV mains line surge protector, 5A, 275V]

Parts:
F1: 5AT; Fuseholder5x20_horiz_open_lateral_Type-II
J1: Conn_01x03_Female; MOV_Surge_Protector
MK1, MK2, MK3, MK4: Mounting_Hole_PAD; SolderWirePad_single_1-5mmDrill
RV1: Littelfuse V20H275P; RV_Disc_D21.5_W5.6_P10

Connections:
unnamed: F1.1, J1.3, RV1.1
unnamed: F1.2, J1.1
unnamed: J1.2, RV1.2
unnamed: MK1.1, MK2.1, MK3.1, MK4.1

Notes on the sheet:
L_Prot

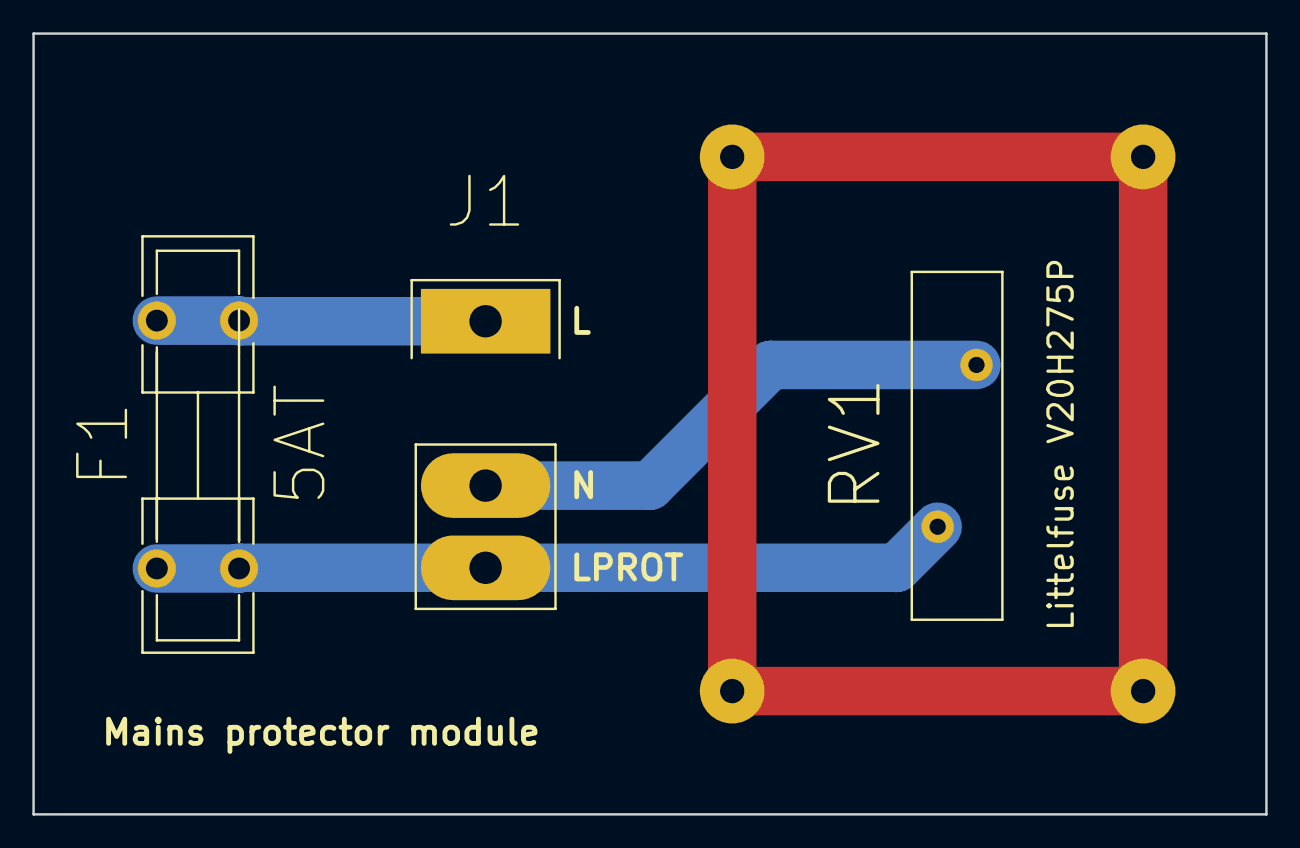
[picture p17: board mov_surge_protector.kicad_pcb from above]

Board: 2 copper layers, 76.2 x 48.3 mm, 7 parts (0 on the bottom side), 4 nets.

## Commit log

2017-03-22 Writing documentation.
    [environment.fcstd, room.obj, room_current.blend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]
2017-03-22 Revising documentation.
    [room_current.blend]
2017-03-23 Fixing doc tree problems.
    [environment.fcstd, room.obj, room_current.blend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]
2017-03-23 Fixing source tree problems.
    [environment.fcstd, room.obj, room_current.blend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]
2017-03-31 Developing front panel (ui).
    [#controller_box_front-panel.dxf, controller_box_front-panel.dxf]
2017-03-31 Revising drawings.
    [#controller_box_front-panel.dxf, controller_box_front-panel.dxf]
2017-04-02 Revising UI drawing.
    [controller_box_front-panel.dxf]
2017-04-15 Creating schematics.
    [_saved_fan-controller_psu.sch, controller.sch, display_driver.sch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]
2017-04-29 Experimentation phase. Investigations re. frequency characteristics of the TL071 OPAMP.
    [fan-controller_research.kicad_pcb, fan-controller_research.sch, sensor_interface.sch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]
2017-05-01 Frequency characteristics: Signal transformer.
    [fan-controller_research.sch, sensor_interface.sch, test_frequecy-transfer_ T60403-K5032-X102_01.sch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]
2017-05-06 Developing 15000Hz filter.
    [fan-controller_research.sch, test_frequecy-transfer_ T60403-K5032-X102_01.sch, test_frequecy-transfer_filter_15000_01.sch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]
2017-05-08 Annotating schematics: 15000 Hz research filter
    [test_frequecy-transfer_ T60403-K5032-X102_01.sch, test_frequecy-transfer_filter_15000_01.sch, test_frequecy-transfer_tl071_01.sch]
2017-07-03 Communication system
    [BOM.csv, Group Delay.csv, Input Impedance Magnitude.csv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]
2017-07-03 Communication system: Starting oscillator modules.
    [bp-25k.bom.ods]
2017-07-05 Comms, oscillator, 25kHz
    [digikey_636347797737312910__5333136.csv, digikey_636347797737312910__5333136.ods, digikey_636347797737312910__5333136.xls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]
2017-07-06 Comms, Oscillator, 25k -> Finalized
    [osc_25k-B.Cu.gbl, osc_25k-B.Fab.gbr, osc_25k-B.Mask.gbs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]
2017-07-06 Minor corrections.
    [osc_25k.sch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]
2017-07-06 Minor changes.
    [osc_25k.kicad_pcb]
2017-07-12 Comms: Osc_25k: Finalized Comms: Detector
    [detector.kicad_pcb, detector.sch, osc_25k.sch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]
2017-07-16 Comms: Detector module
    [detector.kicad_pcb]
2017-08-14 Writing documentation. Chose I2C communication protocol for all stakeholders.
2017-08-17 Reorganized drawings. Writing documentation.
    [comms.sch, comms_analog-sig-switch_4066.sch, comms_osc_15.sch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]
2017-08-18 Modifying surge protection.
    [surge-protect_comms.sch, surge-protect_power-supply_mains.sch, surge-protect_power-supply_periphery.sch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]
2018-01-27 Reorganized file tree. Developing circuitry.
    [BOM.csv, Group Delay.csv, Input Impedance Magnitude.csv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]
2018-01-27 PDF render
    [barrier.sch, comms.sch, controller.sch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]
2018-03-04 Developing and integrating comms i/o router.
    [barrier.sch, comms.sch, controller.sch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]
2018-07-07 Annotation and DRC rule check
    [barrier.sch, comms.sch, controller.sch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]
2018-07-08 Redesign, signalling.
    [barrier.sch, comms.sch, controller.sch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]
2018-07-26 Revisions and simplifications
    [barrier.sch, comms.sch, controller.sch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]
2018-07-28 Diagram cleanup and corrections.
    [barrier.sch, comms.sch, controller.sch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]
2018-08-10 Creating BOM (with ordering)
    [barrier.sch, controller.sch, cpu.sch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]
2018-08-27 Controller: Assigned footprints. Designing PCB.
    [barrier.sch, controller.sch, cpu.sch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]
2018-09-09 Upgraded KiCad to v.5 and made plans compatible Implementing PCB
    [barrier.sch, comms-2018-09-08-15-30-06.sch, comms-2018-09-08-20-57-51.sch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]
2018-09-11 Implementing PCB.
    [controller.kicad_pcb, fan-switch.sch, psu.sch]
